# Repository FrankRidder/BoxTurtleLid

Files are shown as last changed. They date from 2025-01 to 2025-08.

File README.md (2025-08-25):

# BoxTurtleLid
Lid / Hat for BoxTurtle Automated Filament

Simple lid for the BoxTurtle, with an option for filament dryer using a Polydryer base.

Requires 5 additional 2020 360mm aluminum extrusions; printed alternatives are included (see STL/Printable2020Extrusions) if preferred.

Note: The 2020 extrusion for the base front of the lid should either be printed, or some modification will be required to close correctly over the four lightboxes.

Additionally, 5 x 3mm acrylic panels are required.

[Video Here](https://youtube.com/shorts/PpAaRm0n1hM)

## Current status

Design is now complete.

Build photos...

Here's the basic build of the hat, without a heater.

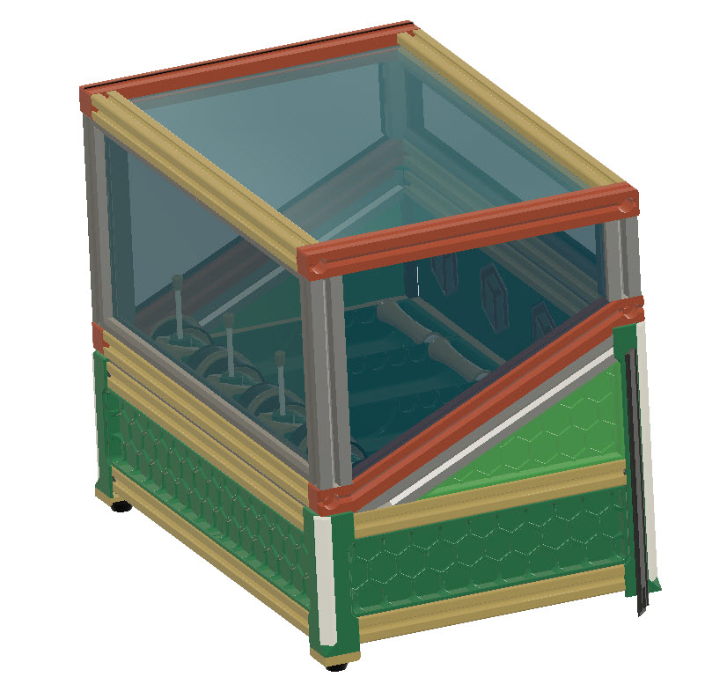
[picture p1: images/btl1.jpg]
 
 

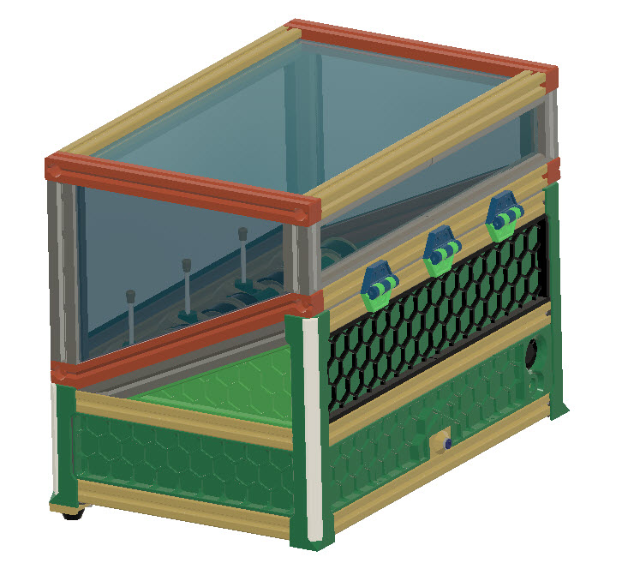
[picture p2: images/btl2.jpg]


The five long extrusions may be 3d printed if required (see stl/Printable2020Extrusions)
All other components are printed. (I'd suggest ABS or ASA if using heater).

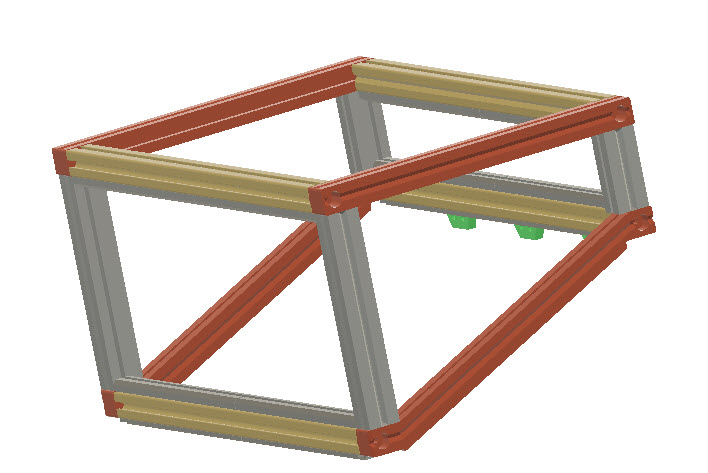
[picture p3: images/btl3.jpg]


The build requires the replacement of the two rear corners with longer versions

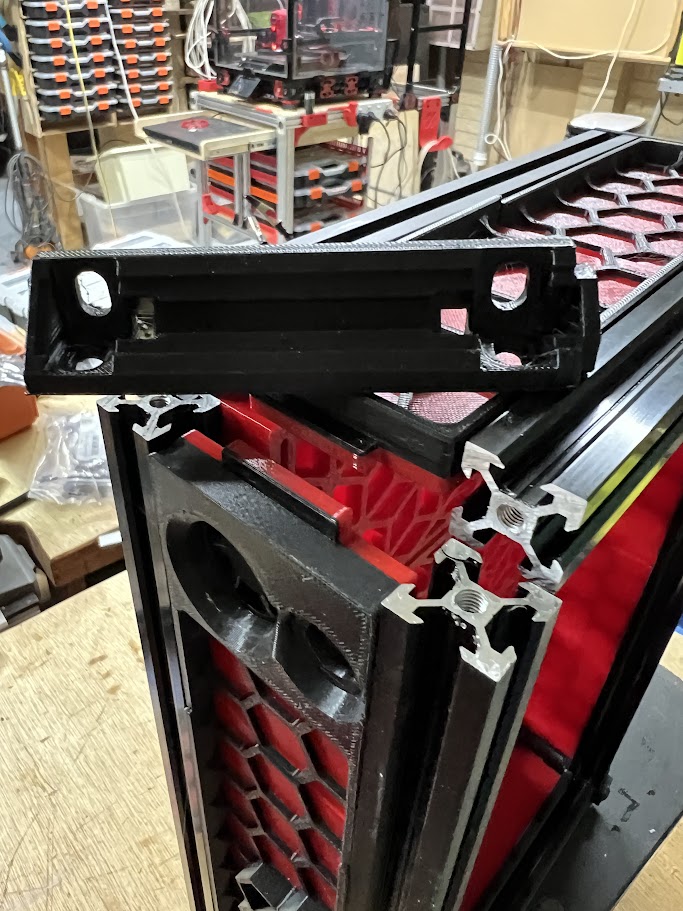
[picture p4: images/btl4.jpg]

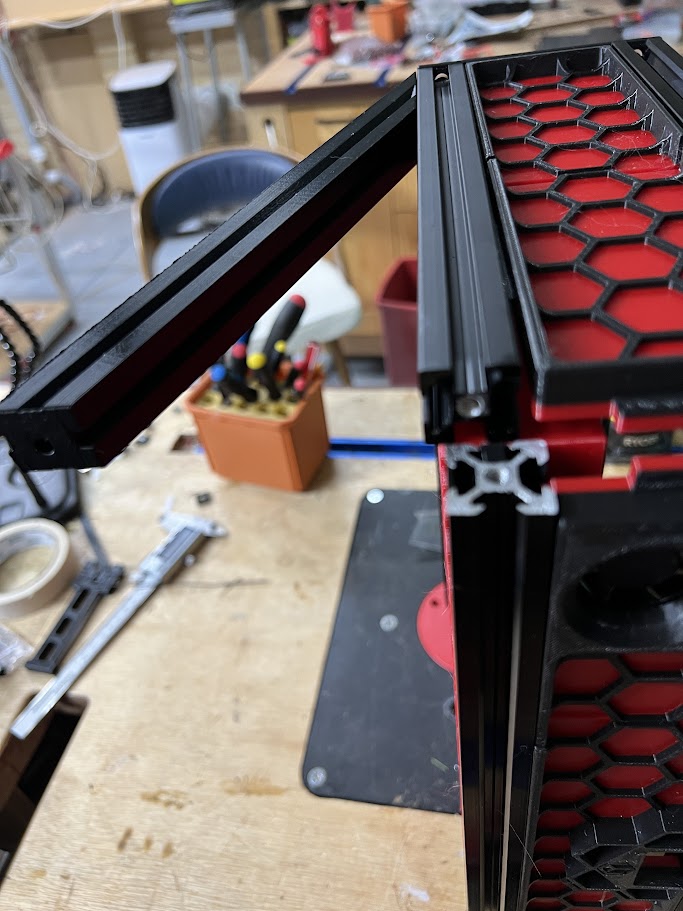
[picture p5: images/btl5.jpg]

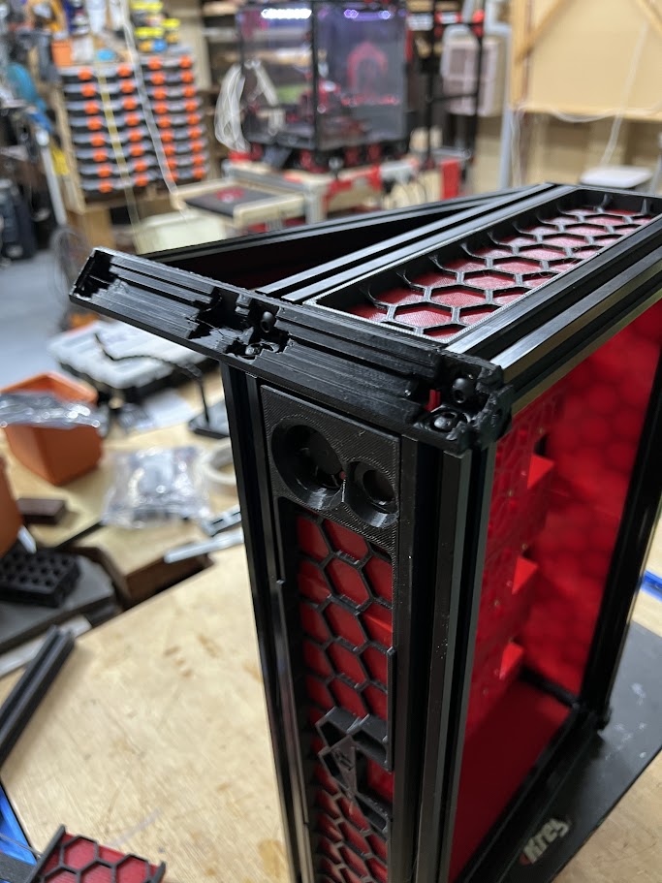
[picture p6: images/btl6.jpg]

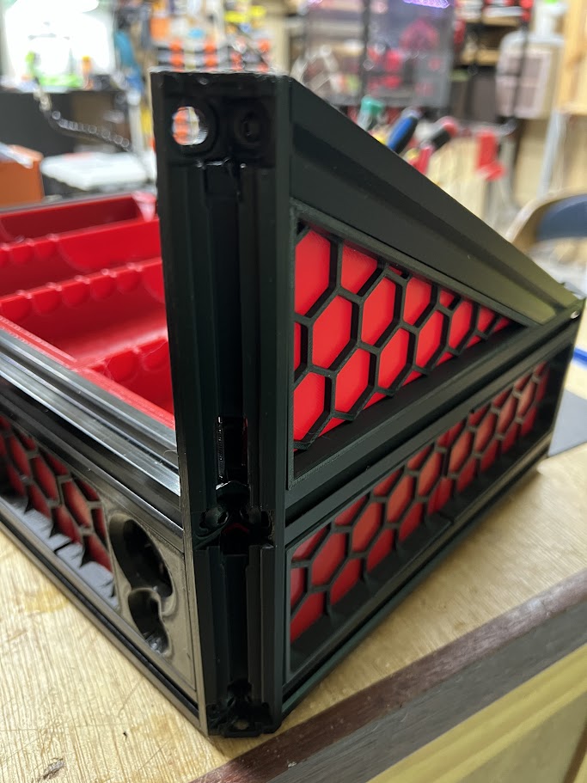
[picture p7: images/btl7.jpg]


An additional rear panel(s) are provided - along with the triangular side panels. 

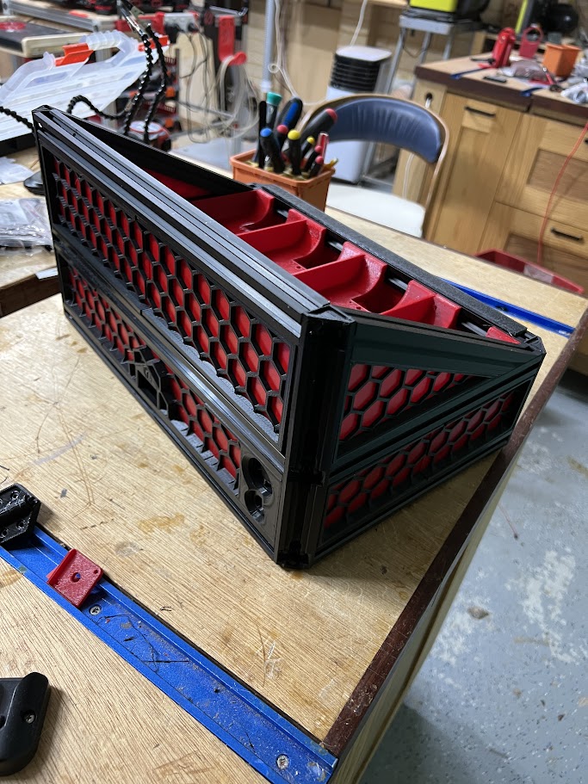
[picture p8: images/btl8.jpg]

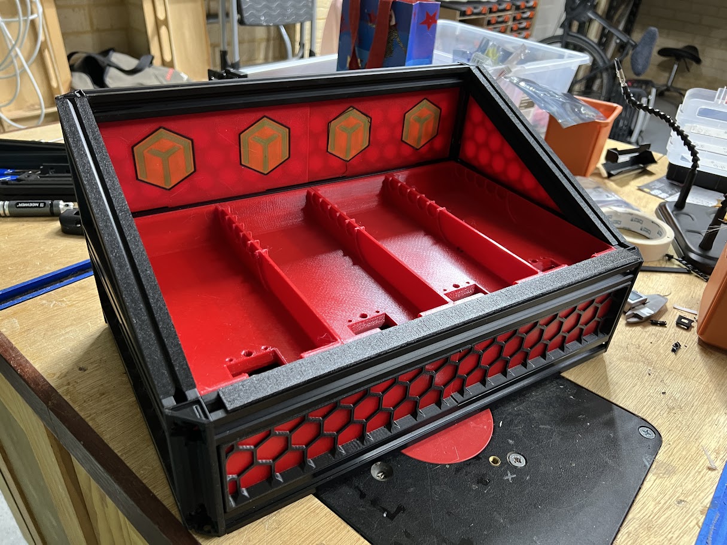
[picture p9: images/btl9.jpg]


If making the heater version, then these are replaceable using magnets. See video - 
[Video Here](https://youtube.com/shorts/PpAaRm0n1hM)

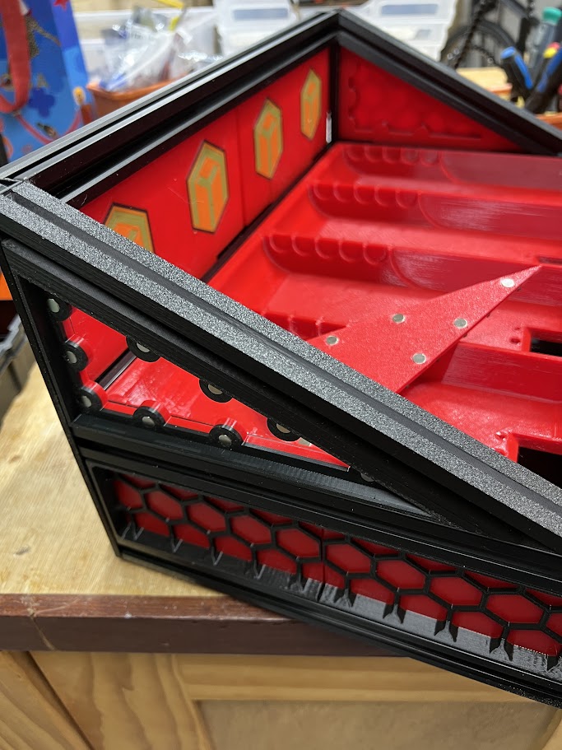
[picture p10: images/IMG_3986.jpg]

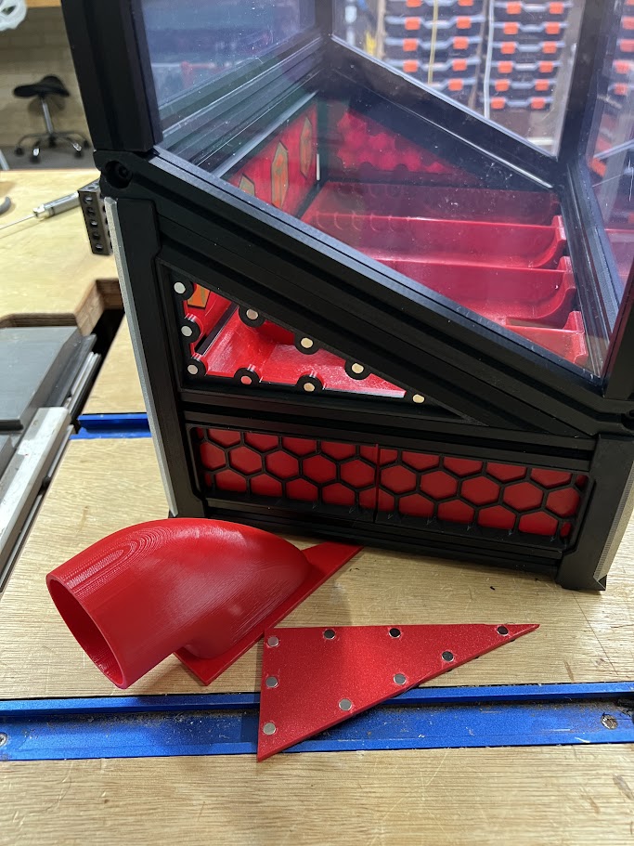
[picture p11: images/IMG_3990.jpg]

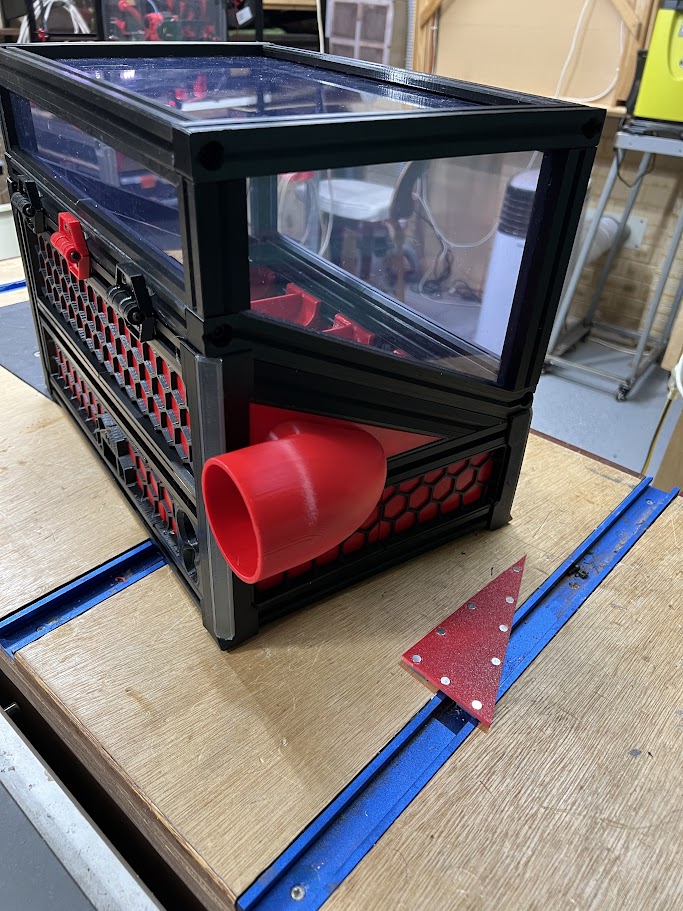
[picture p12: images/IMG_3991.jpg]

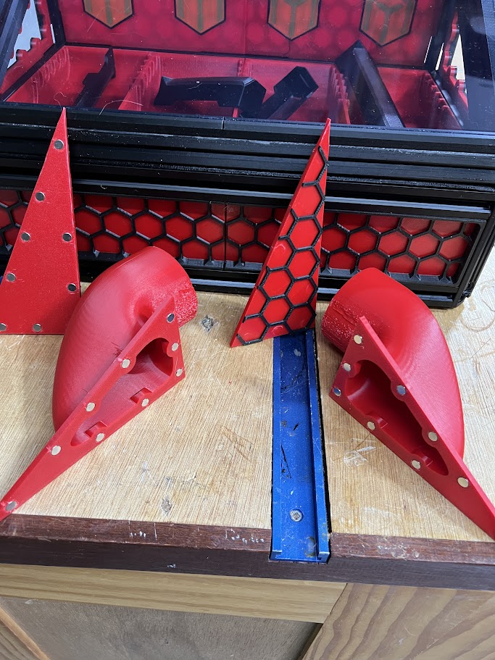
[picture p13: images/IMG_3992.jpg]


The heater is mounted on the rear just above the outbound PTFE tube on a clipped-on table.

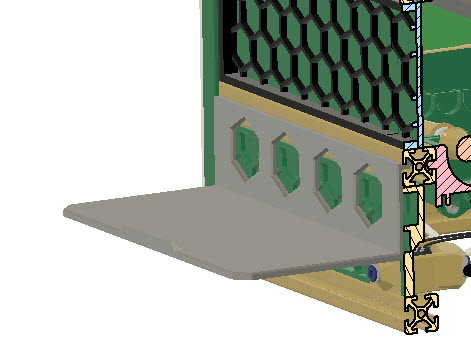
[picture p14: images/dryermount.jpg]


---

## BOM

- 4 x 2020 Extrusion 360mm (Note: 5th on should be printed, the others can optionally be printed - see stl's)
> 3mm Clear acylic panel cut as follows:
- Top: 370 x 225
- Front: 370 x 154
- Rear: 370 x 54
- Sides(x2): 216(topedge) x 165 (BackEdge) x 66 (FrontEdge) x 232 (SlantedBase)

### Screws..

- 6x m3 8mm
- 6x m3 8mm
- 2x m3 heatset inserts (12 when using printed extrusion, 24 when using the printed extrusion with holes for hinges)

### Hinges:

- 6x m3 15mm
- 12x m3 tnuts (non when using printed extrusion with holes)
- 12x m3 6mm

### Heater addition (if used)

- 54 x 6x3 magnets (cheap ones - neodymium magnets NOT needed)

### Bottom Cover (if used)

- 28x 6x3 magnets
- 14x m3 8mm screws
- 14x m3 tnuts

---
## Print Notes

Note that several of the STL require the addition of supports. Alignment and addition of supports are left to the user.

## Build Instructions

### BT modifications

1. Place an m3 heat insert into the two angled 2020 pieces, as well as any printed extrusions, in the ends, as well as in the holes for hinges.

2. Remove one of the rear legs, this will be replaced.


Before replacing, insert the angular 2020 looking piece into the 2020 extrusion as show.



3. Insert the triangular side panel.

4. Ensure the new longer leg is on the correct side. The top hole which connects to the heatset insert is smaller than the other holes.

Replace the leg.



NOTE: The insertion of lights, and covering of the leg is the same as the original BoxTurtle instruction (only longer) - so these details aren't covered here.

5. Repeat steps (2-4) for the other rear leg.

6. Insert the rear panel(s) and attach the top 2020 extrusion



7. Clip the TPU seals into the front and rear 2020 extrusions. This is a simple press fit.

### Top Hat



1. The two sidebars can be screwed into the lower 2020 extrusions as shown

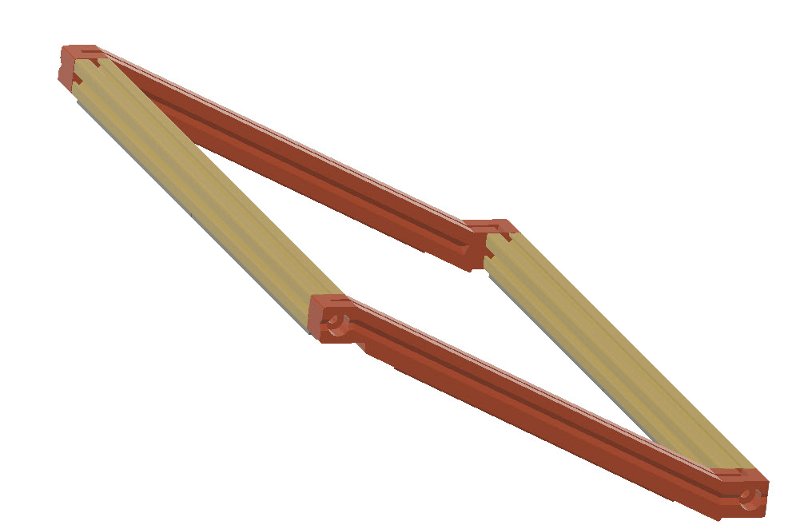
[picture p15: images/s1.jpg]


2. The two rear-uprights print in a U shape, for insertion into the top and bottom 2020 extrusions.

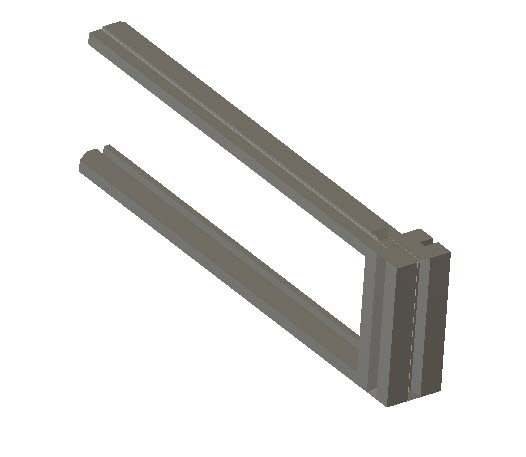
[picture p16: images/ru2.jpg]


Insert as shown below - inserting the rear clear panel at this point.

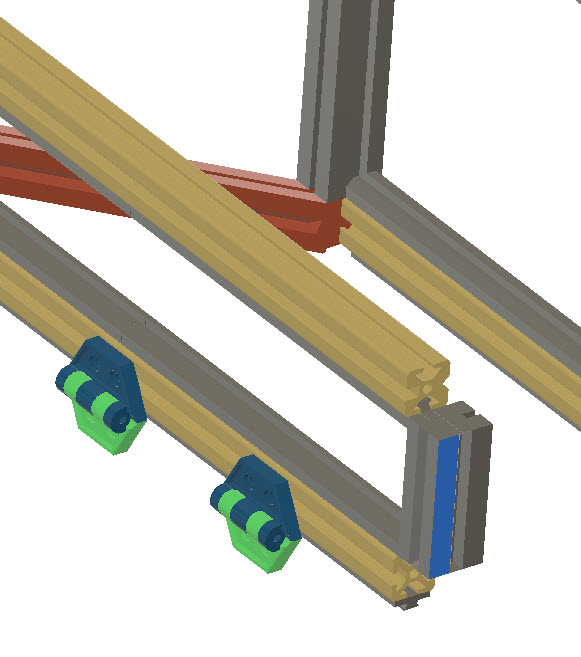
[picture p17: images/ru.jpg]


3. Repeat for the front-uprights inserting the front clear panel at the same time.

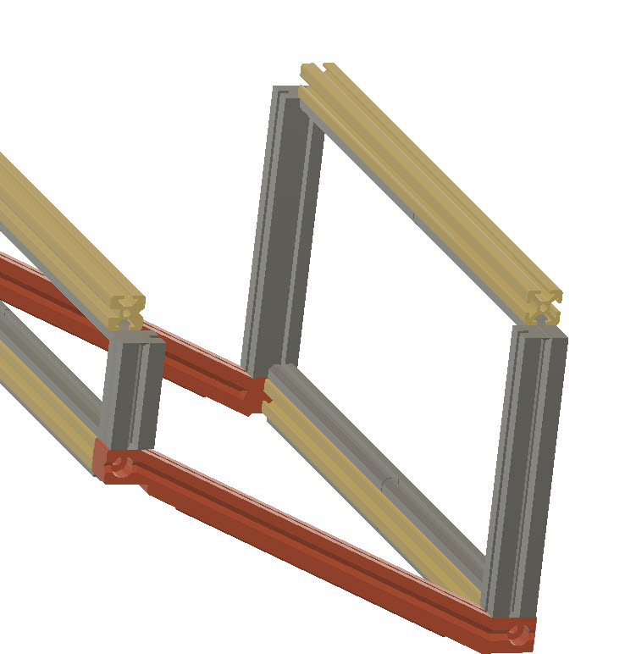
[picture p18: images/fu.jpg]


4. Insert the left panel, and attach the left HatSideBar (upper bar), this screws into the two 2020 extrusions

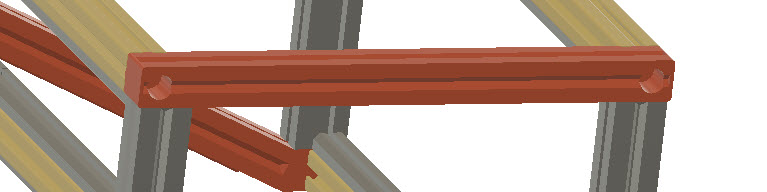
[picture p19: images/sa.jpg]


5. Finally, insert the top and remaining side clear panels, the right HatSideBar can now be attached.
Note: This will require some of the surrounding bolts to be loosened to allow the panels to fit into the sidebar.

6. Re-tighten the bolts.

### Base cover

The stl/BaseCover folder contains files for creating a simple magnetic snap-on base cover.

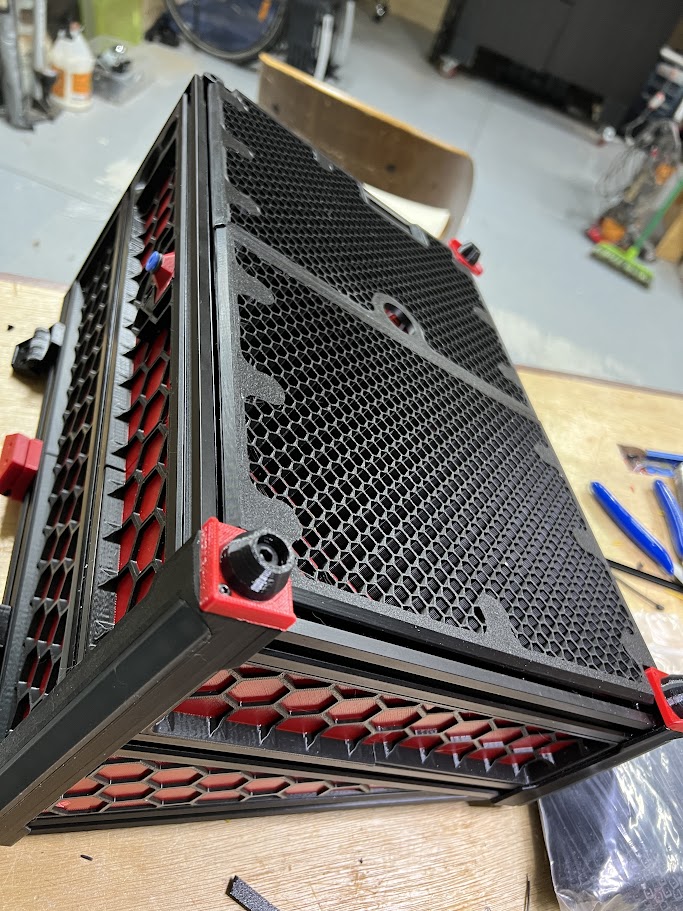
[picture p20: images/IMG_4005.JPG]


[Video Here](https://youtube.com/shorts/HE4AY-ndGrg)

The Base.3mf file contains the slicer settings needed to create the hex pattern on the base.

Alternatively, open the left stl file in a slicer and split-to-parts. 
The inner part needs modifying to have 

- zero wall-loops, top-shell-layers and bottom-shell-layers.
- Sparse-Infill pattern: Honeycomb at 10%

Repeat this for the right stl.

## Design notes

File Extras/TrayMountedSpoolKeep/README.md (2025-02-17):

# BoxTurtleLid - EXTRAS

# Got wobbly spools - here's a simple fix to keep them in place.

Designed for 62mm width spools, the fusion parameters may be changed to generate other widths.

72mm STL also included (I found this suitable for almost all spools)

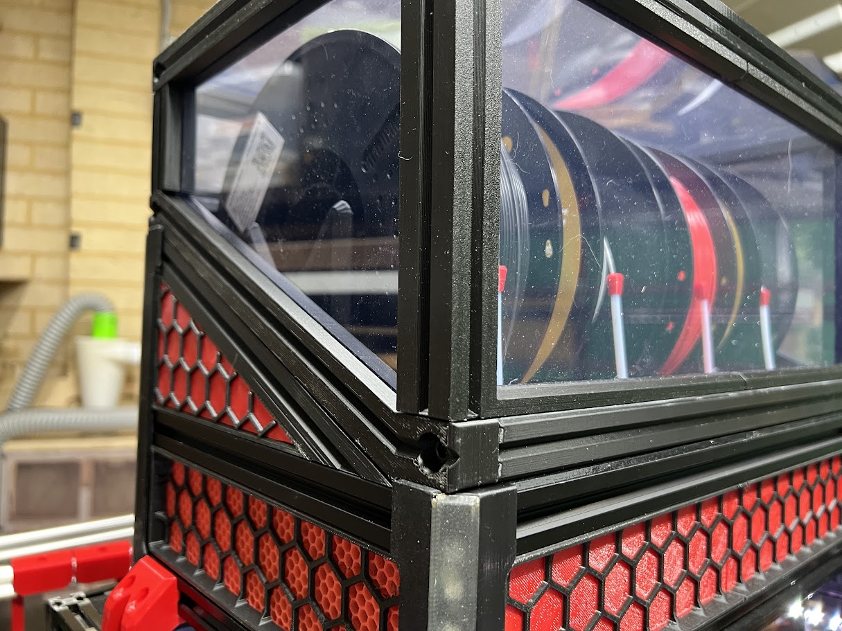
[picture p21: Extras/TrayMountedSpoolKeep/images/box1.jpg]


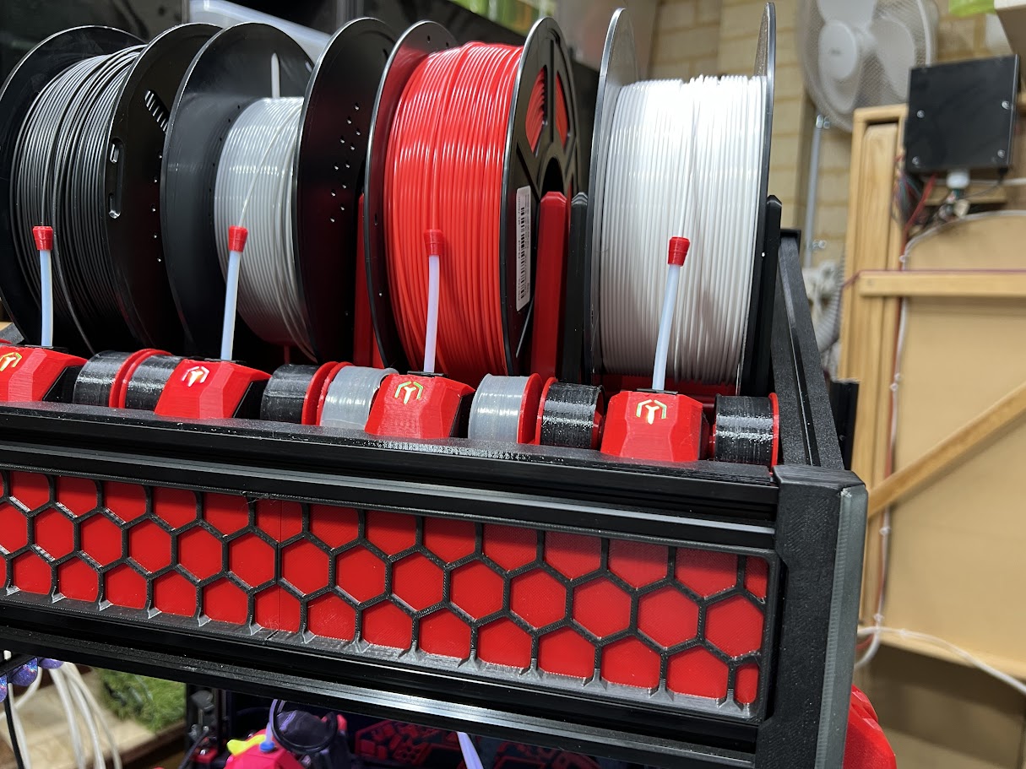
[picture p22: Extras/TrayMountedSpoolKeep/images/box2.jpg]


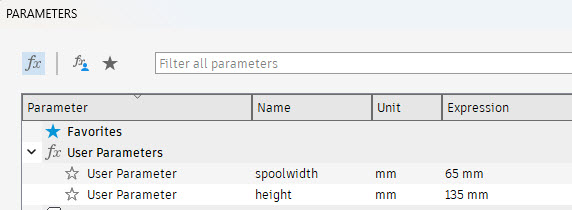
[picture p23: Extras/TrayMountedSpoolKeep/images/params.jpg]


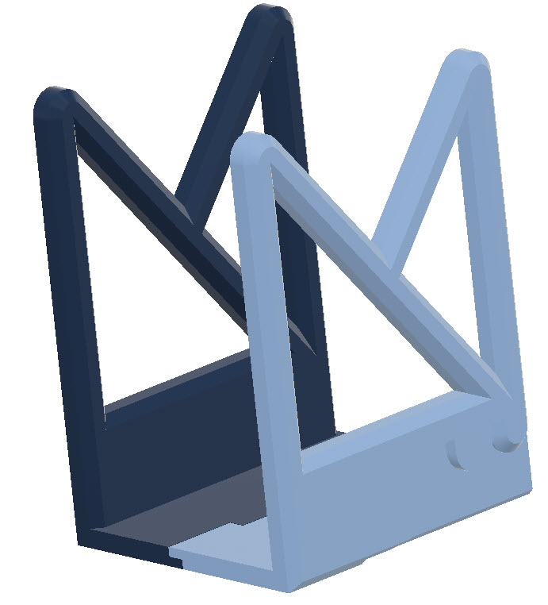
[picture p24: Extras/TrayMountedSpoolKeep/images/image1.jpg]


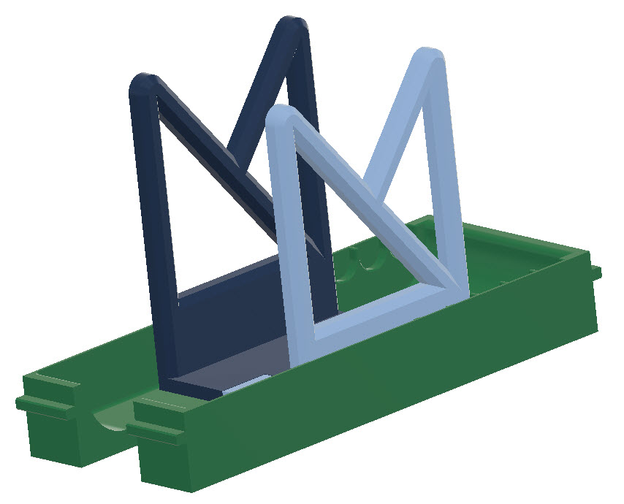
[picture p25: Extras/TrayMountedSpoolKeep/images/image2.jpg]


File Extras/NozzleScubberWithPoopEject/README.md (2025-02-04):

# Gantry Mounted Nozzle Scrubber with poop eject

Here's a design for a nozzle scrubber that ejects poop as needed.

[Video Here](https://youtu.be/P8CdES0VPNM)

The scubber has a moving head riding on 6 small bearings that pushes any poop off the poop-deck during the scrubbing motion.

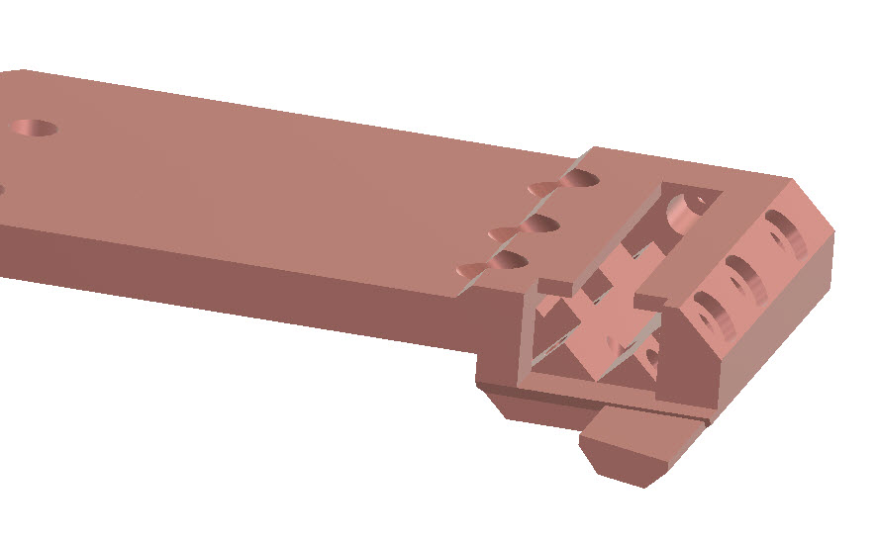
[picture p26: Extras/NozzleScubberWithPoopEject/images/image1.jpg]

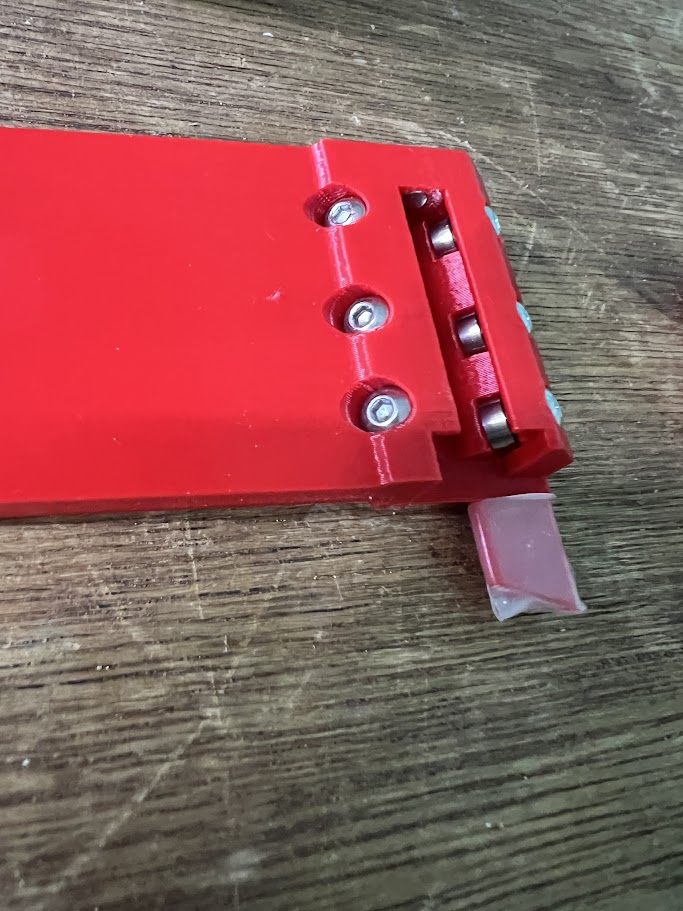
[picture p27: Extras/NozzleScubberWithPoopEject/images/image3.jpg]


# PoopDeck

This is the location for any poop during a filament change. I recommend covering this with a thin layer of silocone.



For example this tape (many similar tapes available) is easy to attach, wrapping like a rubber band around the deck.

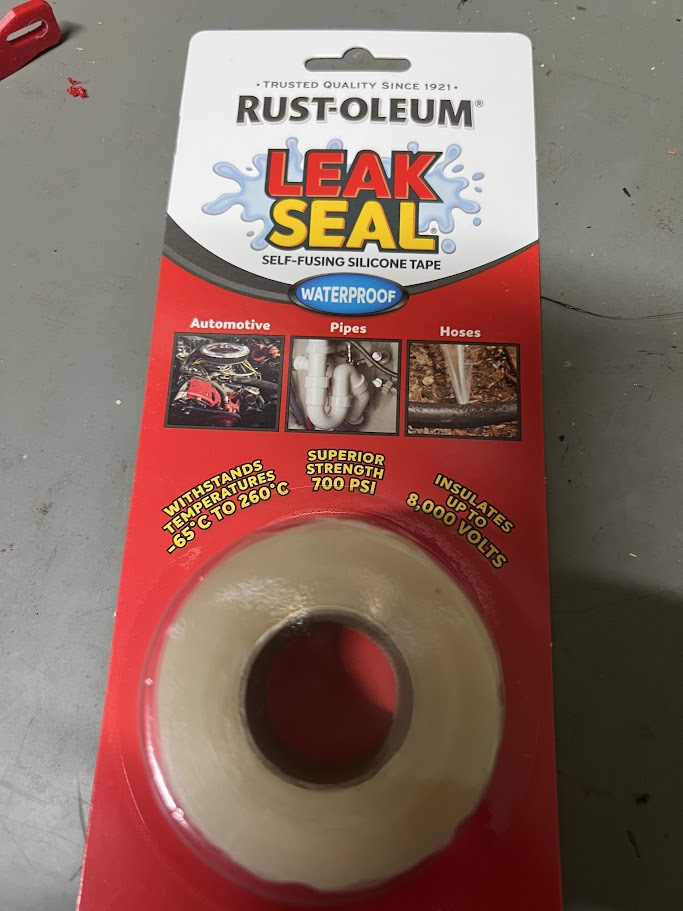
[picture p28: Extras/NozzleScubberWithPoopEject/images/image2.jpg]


# Scrubber

The scrubber I've attached is a standard bambu-labs style silicone brush. Other brush styles can be used, but keep the depth similar.

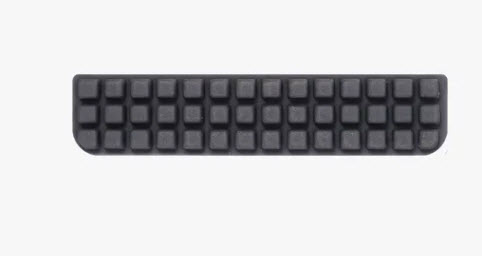
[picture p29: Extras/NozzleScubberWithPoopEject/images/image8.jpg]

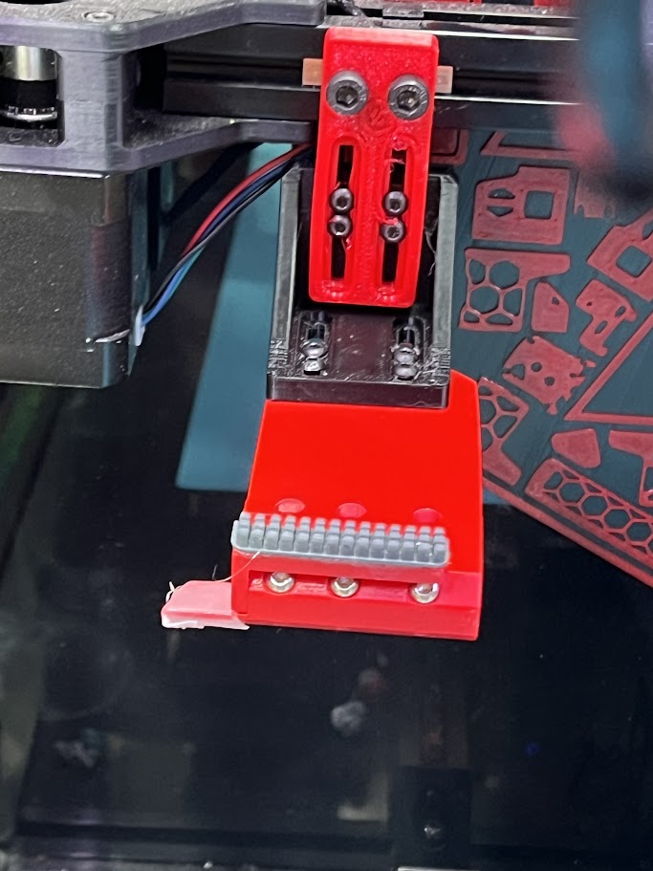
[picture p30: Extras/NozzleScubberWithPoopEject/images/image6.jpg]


# Auto-return

Magnets ensure the scrubber stays in place when not in use. 

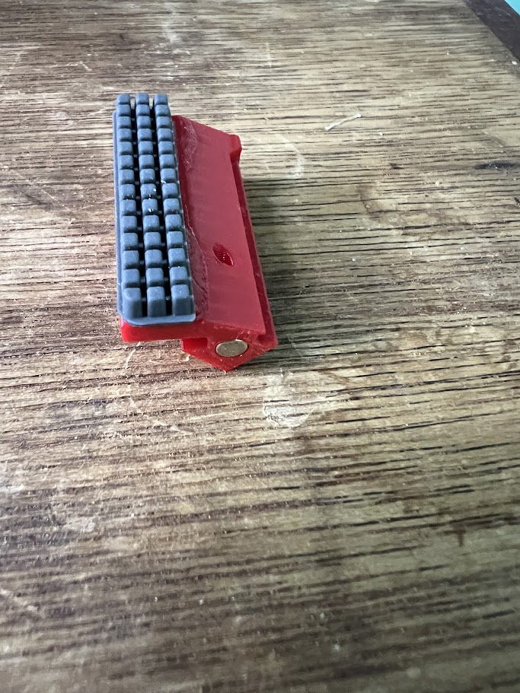
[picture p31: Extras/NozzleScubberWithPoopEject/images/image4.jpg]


# BOM

- 2x 4mmx5.7mm Magnets
- 7x 6mm m3 bolts (holding bearings, and brush stop)
- 8x 10mm m3 bolts (L bracket assembly)
- 2x 10mm m4 bolts
- 2x m4 2020-slidein nuts
- 6x MR63ZZ bearings
- Self-Fusing silicone tape

# Build Notes.

The magnet and bearing holes all have small holes into their bases to allow easy removal if needed.

After sliding on the slider, use a 6mm m3 bolt in the base to stop the slider being removed.

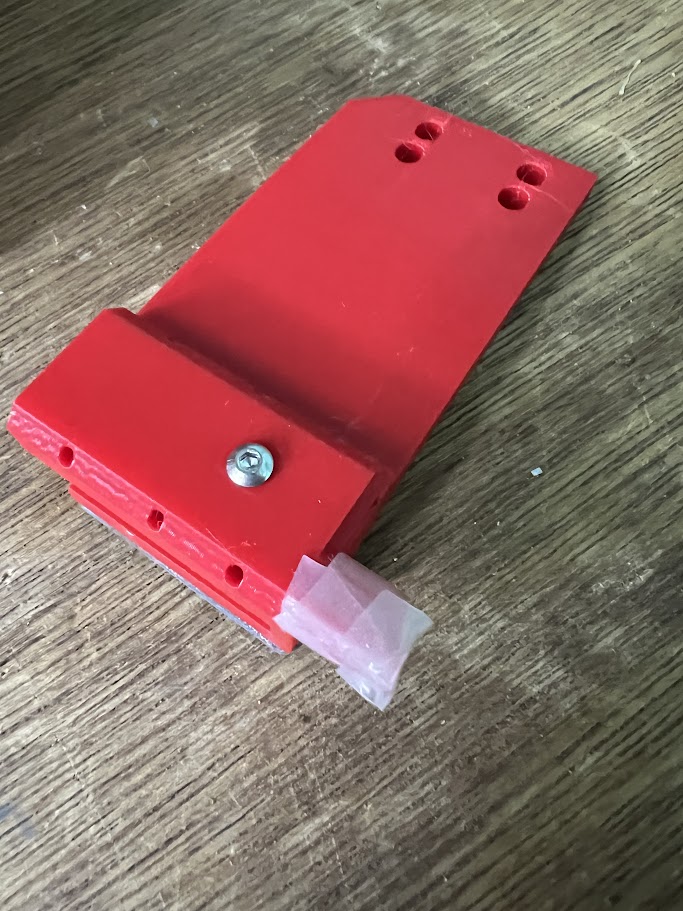
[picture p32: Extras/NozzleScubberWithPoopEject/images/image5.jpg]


A suggested cleannozzle macro is included in the macros/ folder. Modify the x/y positions at the start of the macro as needed.

> [gcode_macro CLEAN_NOZZLE_GANTRY]\
> description: Clean nozzle using sliding gantry brush\
> `#` Define the location where the poop will land, all other locations will be based off\
> `#` this position. It should be the center of the silicone coated poop tray, 5mm left of\
> `#` left edge of the rubber nozzle brush.\
> variable_x_poop: 18\
> variable_y_poop: 300 \
> variable_number_wipes: 3

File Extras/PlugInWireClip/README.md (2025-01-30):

# BoxTurtleLid - EXTRAS

# Plugin wire clip holder

A simple replacement for using zipties to hold down wiring.

My sausage fingers have trouble threading zip-ties, and I like the ability to remove / add wires at any time.

I printed in PETG to give it a little extra flex.

This unit just inserts in using the zip-tie hole to securely clip in. The wires can then be clipped under the top clip part.

If bottom facing mounts required, then just mirror the part in the slicer.

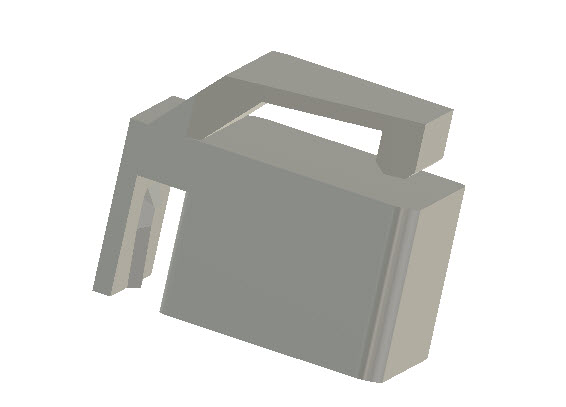
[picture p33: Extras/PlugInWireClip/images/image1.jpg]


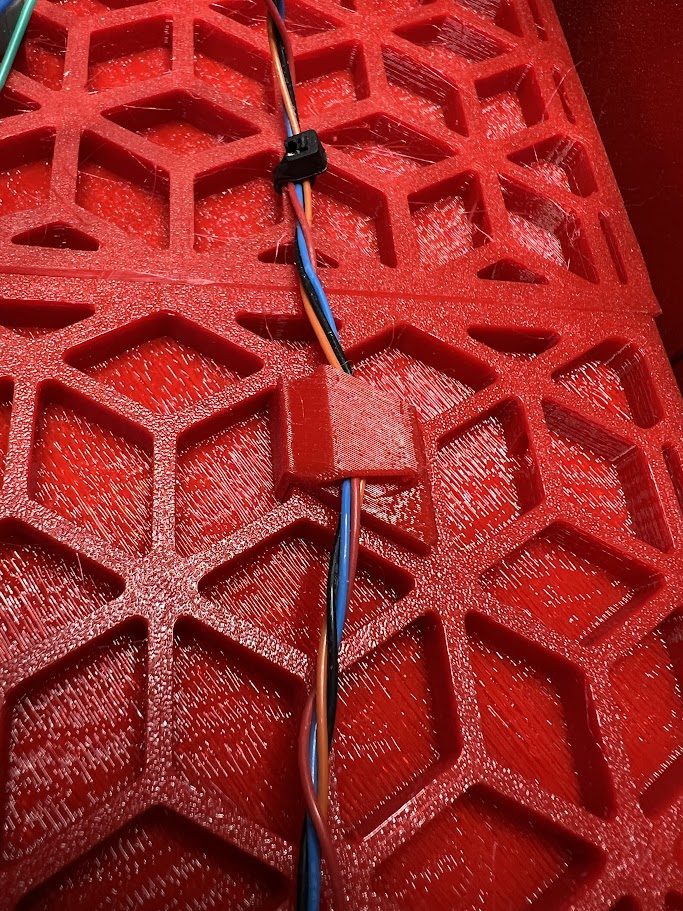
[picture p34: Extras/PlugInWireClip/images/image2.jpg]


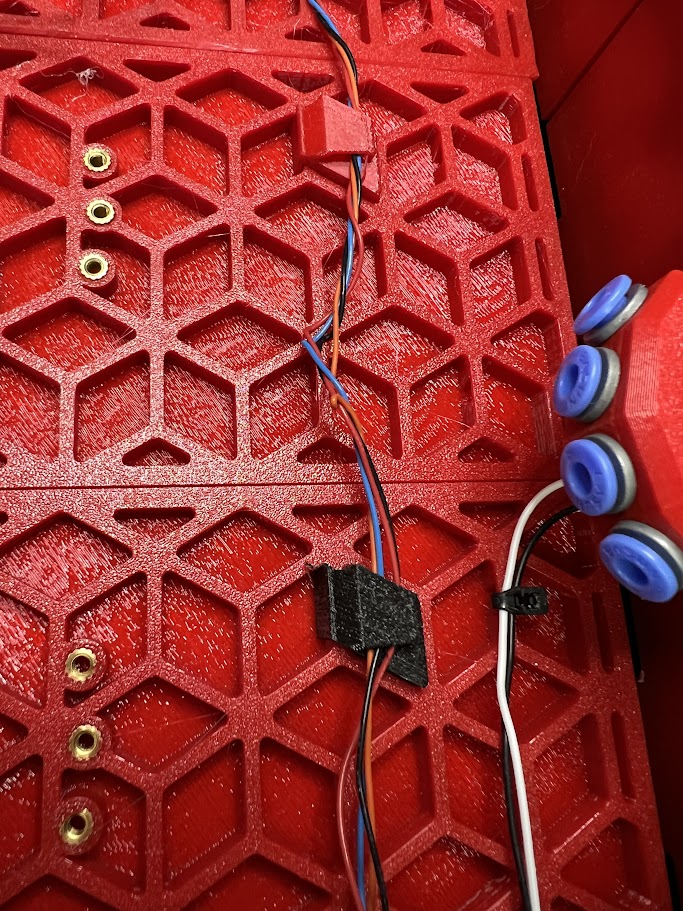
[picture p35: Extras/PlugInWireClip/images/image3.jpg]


[video](https://www.youtube.com/watch?v=fOTQHvDfOQY)

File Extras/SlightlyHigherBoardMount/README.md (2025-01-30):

# BoxTurtleLid - EXTRAS

# Slightly Higher Mounting Board

Here's the slightly raised (lowered?) board mounting, allowing a USB elbow to be fitted.

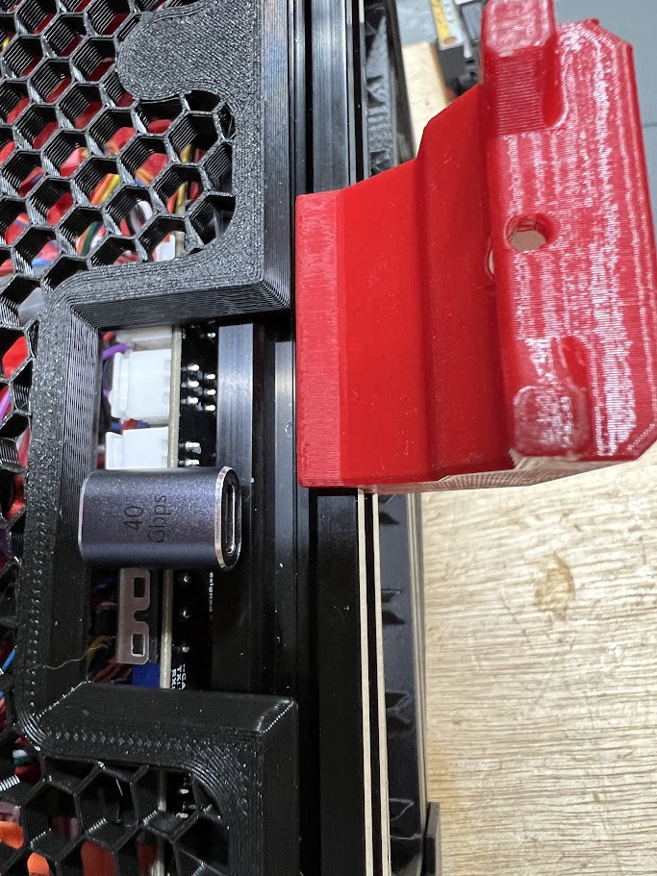
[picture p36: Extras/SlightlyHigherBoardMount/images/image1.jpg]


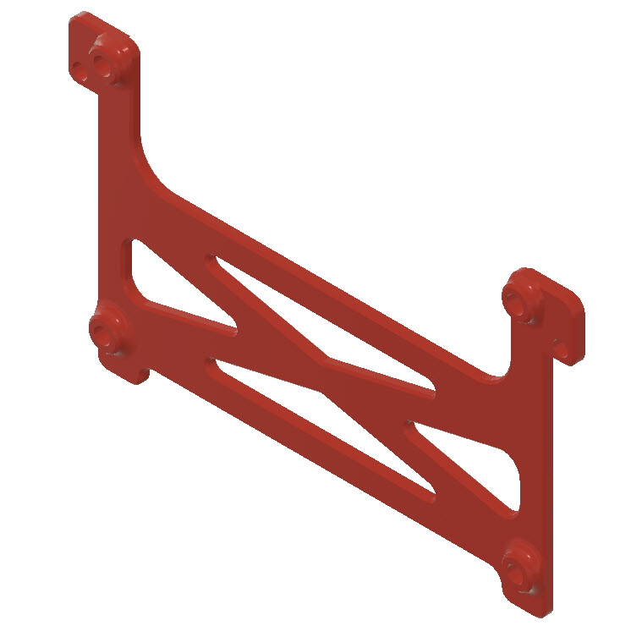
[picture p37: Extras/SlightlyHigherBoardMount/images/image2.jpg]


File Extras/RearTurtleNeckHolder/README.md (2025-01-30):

# BoxTurtleLid - EXTRAS

# Rear Turtle Neck Holder

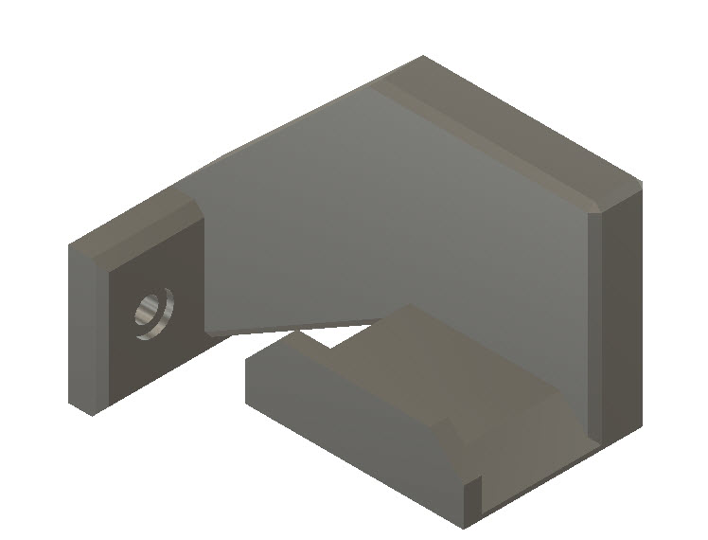
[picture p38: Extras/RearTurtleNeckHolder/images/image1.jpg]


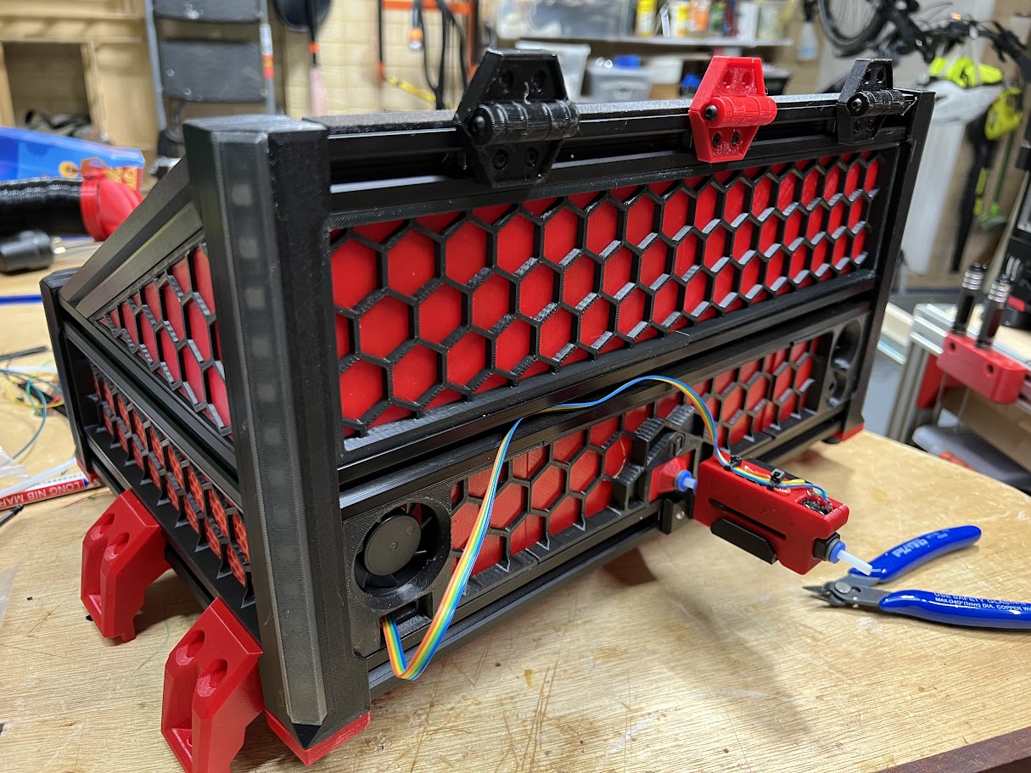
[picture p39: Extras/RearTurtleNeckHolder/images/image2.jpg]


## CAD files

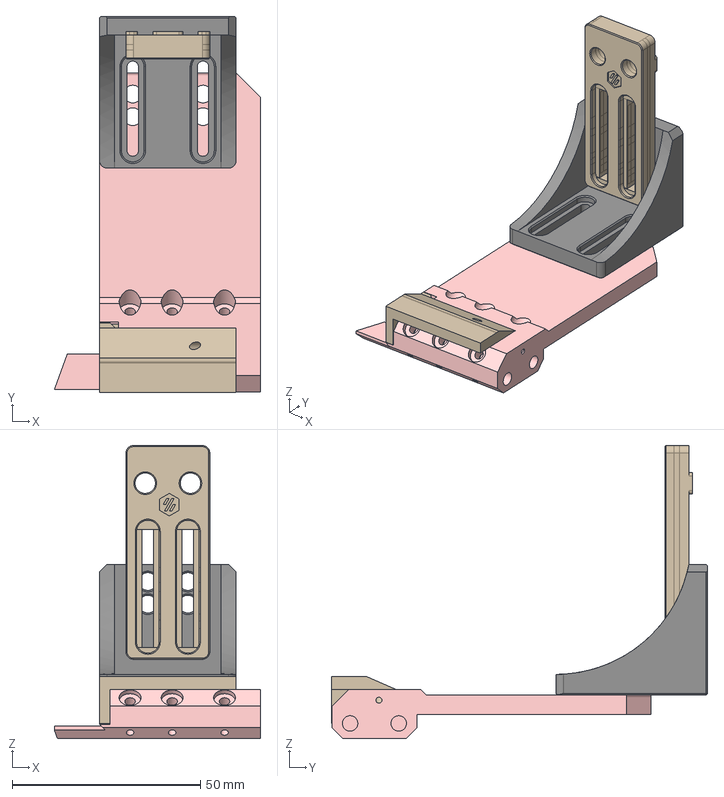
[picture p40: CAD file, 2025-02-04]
Extras/NozzleScubberWithPoopEject/cad/Scrubber Assembly v16.step
54.8 x 99.9 x 77.7 mm
Dock Mount variable Assembly
Dock Mount variable Assembly_1
Slider
Base
Dock Mount variable Assembly_2

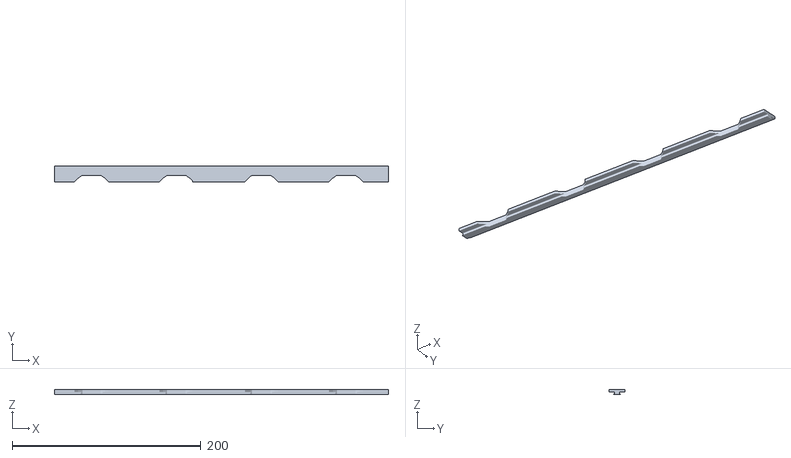
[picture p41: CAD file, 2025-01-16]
stl/tpu_seal(fulllength)_bottom.stl
354.3 x 16.5 x 5.28

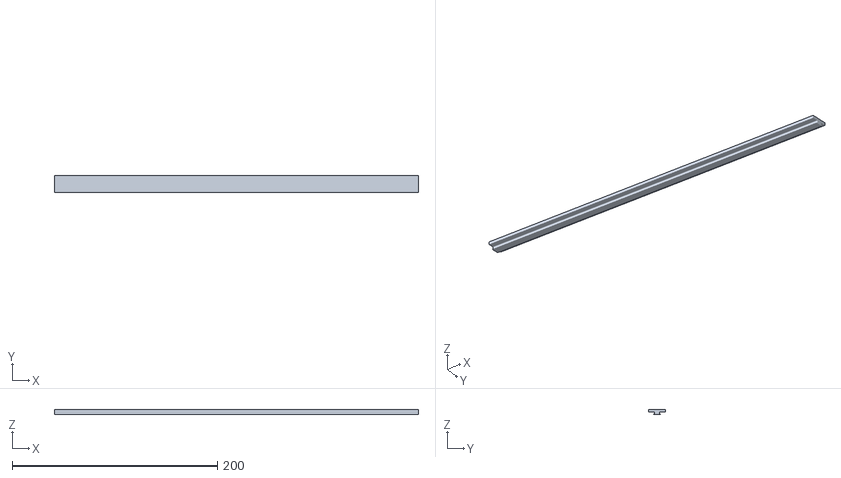
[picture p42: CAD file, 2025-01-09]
stl/tpu_seal(full_length)_top.stl
354.3 x 16.5 x 5.28

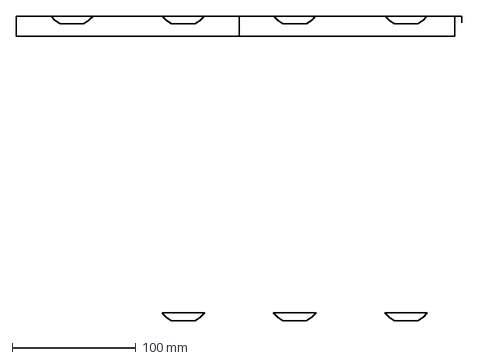
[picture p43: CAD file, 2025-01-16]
cad/tpu_template.dxf
360.0 x 246.5 mm

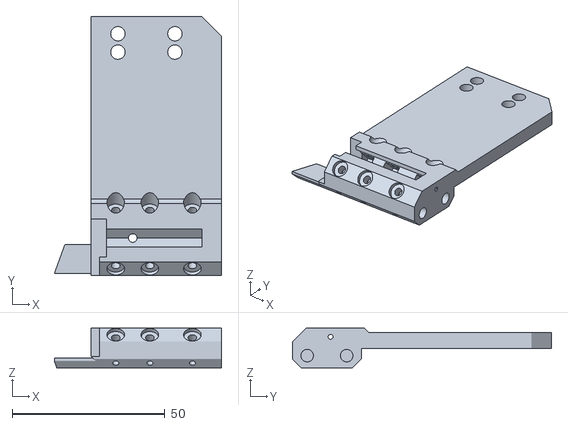
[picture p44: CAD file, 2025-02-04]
Extras/NozzleScubberWithPoopEject/stl/Base.stl
54.8 x 84.7 x 13.0

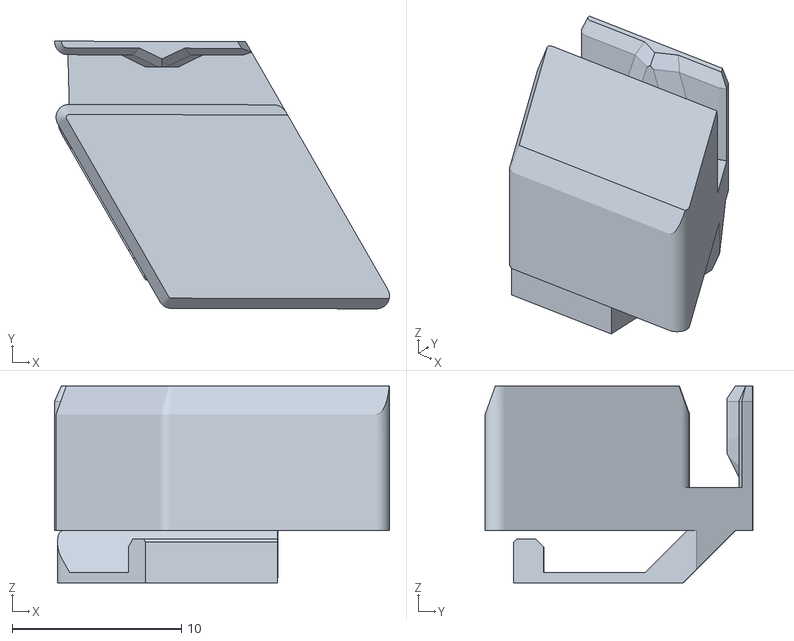
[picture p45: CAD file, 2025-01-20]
Extras/PlugInWireClip/stl/ZipTieReplacement.stl
19.8 x 15.8 x 11.6

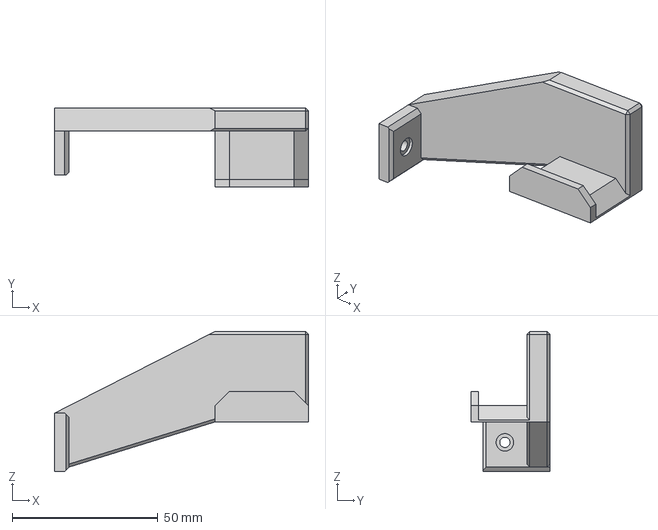
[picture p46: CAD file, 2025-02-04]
Extras/RearTurtleNeckHolder/cad/TurtleNeckHolder v5.step
87.0 x 27.2 x 48.0 mm

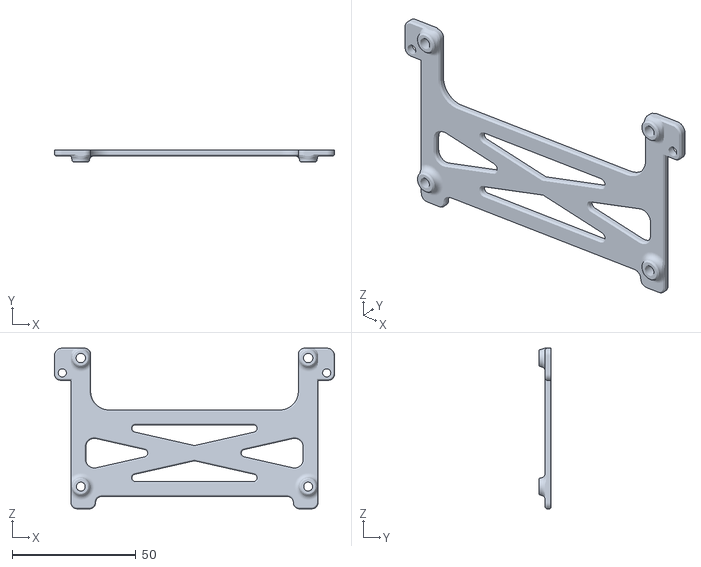
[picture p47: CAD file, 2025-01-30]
Extras/SlightlyHigherBoardMount/stl/Mount.stl
113.3 x 5.00 x 65.0

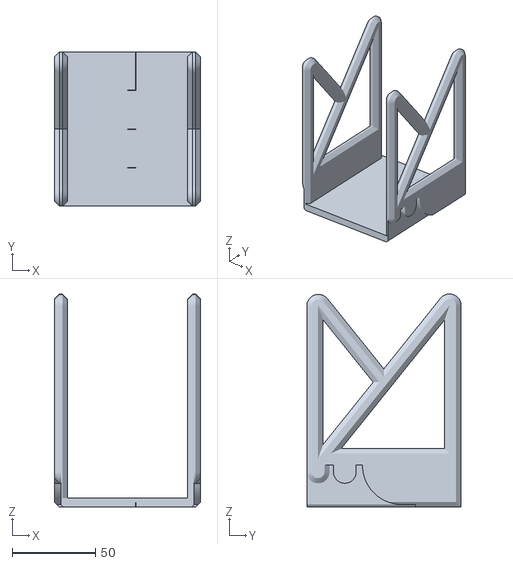
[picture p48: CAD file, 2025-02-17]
Extras/TrayMountedSpoolKeep/stl/TrayMountSpoolKeep_72mm(Split for L-R).stl
87.5 x 92.5 x 127.6

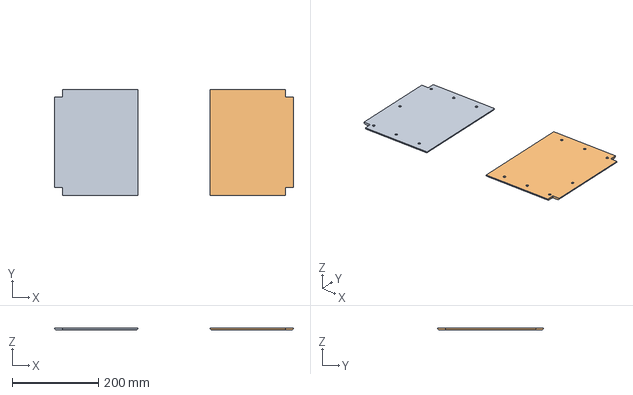
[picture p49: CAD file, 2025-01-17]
stl/BaseCover/Base.3mf
553.6 x 245.5 x 5.00 mm
Base.stl
BaseRight.stl

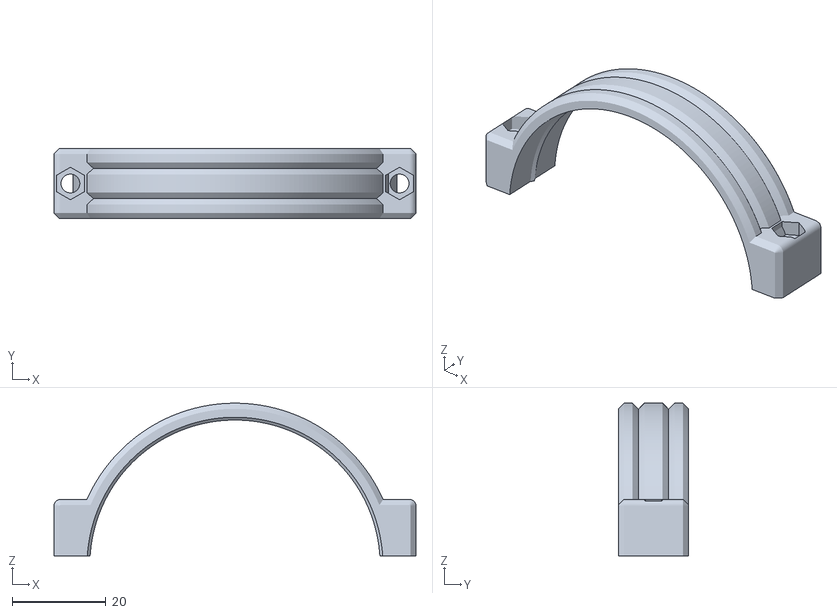
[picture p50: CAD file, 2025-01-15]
stl/HeaterPortVersion/65mmClip2.stl
77.1 x 15.0 x 32.5

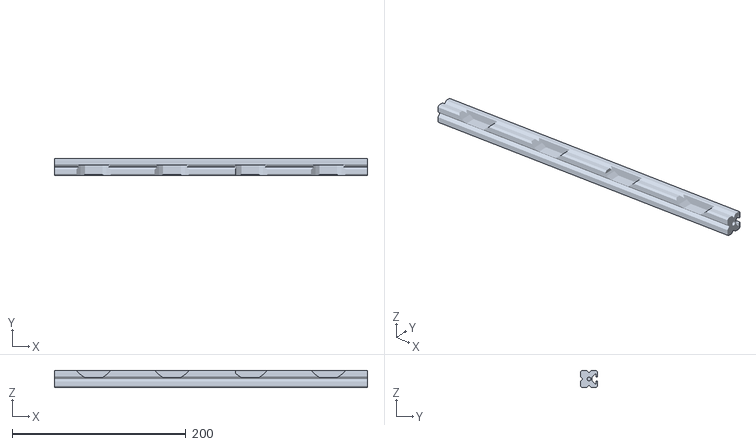
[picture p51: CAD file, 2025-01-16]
stl/Printable2020Extrusions/Printable2020FrontLidBase.stl
360.0 x 20.0 x 20.0

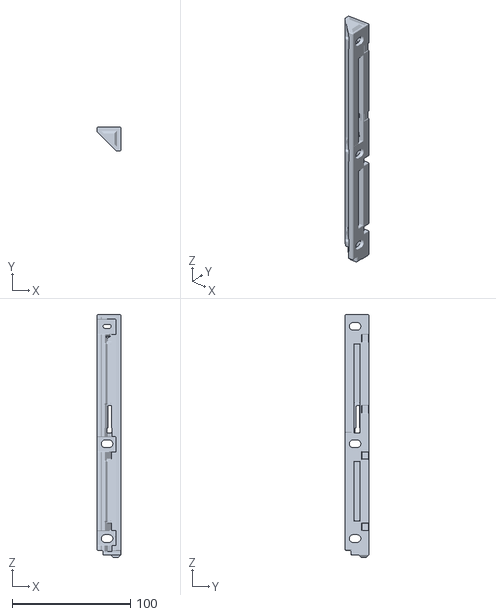
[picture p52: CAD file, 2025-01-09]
stl/RearLegReplacements/RearLidCornerRight.stl
20.0 x 20.0 x 205.2

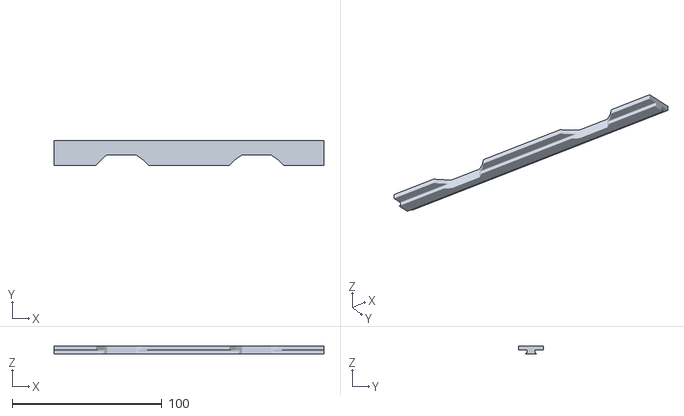
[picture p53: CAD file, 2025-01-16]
stl/tpu_seal_bottom_left.stl
180.0 x 16.5 x 5.28

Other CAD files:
cad/BoxTurtle_UpperSideSkirt_HeaterConnect.step
Extras/NozzleScubberWithPoopEject/stl/Slider.stl
Extras/TrayMountedSpoolKeep/stl/Right_62mm.stl
stl/BaseCover/Holder.stl
Extras/NozzleScubberWithPoopEject/stl/Joint v2.stl
Extras/NozzleScubberWithPoopEject/stl/Vertical mount v3.stl
Extras/RearTurtleNeckHolder/cad/TurtleNeckHolder v5.f3d
Extras/RearTurtleNeckHolder/cad/TurtleNeckHolder.step
Extras/RearTurtleNeckHolder/stl/TurtleNeckHolder.stl
Extras/TrayMountedSpoolKeep/cad/TrayMountedSpoolKeep v5.f3d
Extras/TrayMountedSpoolKeep/stl/Left_62mm.stl
cad/2020Extrusion v7.step
stl/BaseCover/BaseLeft.3mf
stl/BaseCover/BaseLeft.stl
stl/BaseCover/BaseRight.stl
stl/FrontUprightLeft.stl
stl/FrontUprightRight.stl
stl/HatSideBarLeft.stl
stl/HatSideBarRight.stl
stl/HeaterPortVersion/65mmClip1.stl
stl/HeaterPortVersion/HeaterPlate (1).stl
stl/HeaterPortVersion/NoHeaterPlate.stl
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

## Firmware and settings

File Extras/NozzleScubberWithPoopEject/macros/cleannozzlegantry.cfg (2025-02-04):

[gcode_macro CLEAN_NOZZLE_GANTRY]
description: Clean nozzle using sliding gantry brush
# Define the location where the poop will land, all other locations will be based off
# this position. It should be the center of the silicone coated poop tray, 5mm left of
# left edge of the rubber nozzle brush.
variable_x_poop: 18
variable_y_poop: 300 
variable_travel_speed: 12000
variable_wipe_speed_fast: 12000
variable_wipe_speed_slow: 6000
variable_poop_to_brush: 5
variable_brush_width:40 
variable_number_wipes: 3
gcode:
   # Start point is far right - to ensure and excess poop gets pushed
   {% set start_x = (x_poop + poop_to_brush + brush_width) %} 
   {% set full_wipe = (poop_to_brush + brush_width) %} 
   SAVE_GCODE_STATE NAME=clean_nozzle_gantry
   G91                                         # Relative
   G1 Z-5                                      # Move up a tad

   G90                                         # Absolute

# Start the cleanup

   RESPOND TYPE=command MSG='CLEANNOZ: move - X{start_x}'
   G1 X{x_poop} Y{y_poop} F{travel_speed}     # Move to start area
   G91                                         # Relative

   G1 X{full_wipe} F{wipe_speed_slow}
   {% for _ in range(number_wipes) %}
      G1 X-{full_wipe} F{wipe_speed_fast}      # Move Left
      
      G1 X-10 F{wipe_speed_fast}               # Move away from poop
      {% for _a in range(5) %}                 # And wiggle anything off
         G1 X6 F{wipe_speed_fast}
         G1 X-6 F{wipe_speed_slow}
      {% endfor %}
      G1 X10 F{wipe_speed_fast}                # Move Back 

      G1 X{full_wipe} F{wipe_speed_fast}          # Move Right
   {% endfor %}
  
# Final move slow to right to ensure brush goes back in place

   G1 X-{full_wipe} F{wipe_speed_fast}         # Move Left
   G1 X{full_wipe} F{wipe_speed_slow}         # Move Right

   G1 Y-5 F{wipe_speed_slow}                  # Move forward away from brush

   G90                                        # Absolute
   RESTORE_GCODE_STATE NAME=clean_nozzle_gantry

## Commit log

2025-01-09 Initial load
    [FrontUprightLeft.stl, FrontUprightRight.stl, HatSideBarLeft.stl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]
2025-01-16 Allow for lights in 2020 extrusion and seal
    [Printable2020FrontLidBase.stl, tpu_seal(full_length)_top.stl, tpu_seal(fulllength)_bottom.stl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]
2025-01-18 Mod AFC mount
2025-01-19 Mod ziptie
    [ZipTieReplacement.stl]
2025-01-30 Extras added
    [Left.stl, Mount.stl, Right.stl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]
2025-02-04 Added Nozzle Scrubber to Extras
    [Base.stl, Joint v2.stl, Scrubber Assembly v16.step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]
2025-02-17 inlude 72mm version of spoolkeep
    [Left_62mm.stl, Right_62mm.stl, TrayMountSpoolKeep_72mm(Split for L-R).stl]
2025-08-19 Update README.md
    Correct BOM and fix broken image
